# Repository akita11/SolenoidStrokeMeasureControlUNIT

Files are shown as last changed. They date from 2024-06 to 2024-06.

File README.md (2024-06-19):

# SolenoidStokeMeasureControl UNIT

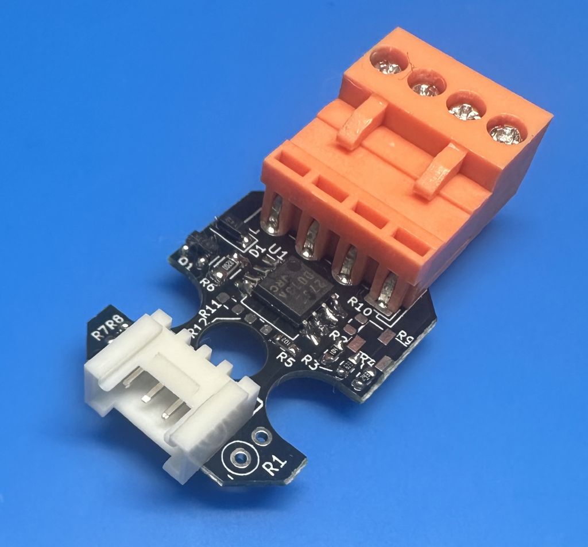
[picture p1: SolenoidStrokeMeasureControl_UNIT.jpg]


ソレノイドのストローク位置によってインダクタンスが変化し、PWM制御時の電流波形が変化することを利用して、ソレノイドのPWM制御とストローク位置の計測（推定）を同時に行うための回路です。
（基板形状が「[M5Stack用VH3.96-4ピンユニット[U020]](https://www.switch-science.com/products/4055)」と同一のため、そのケースを使うことができます。）

**【注意：重要】**
実際の制御・計測の動作には、ソレノイドごとに特性の計測を行う必要があり、また特性の個体差、温度特性なども考慮する必要があります。そのため、**「これを使ってサンプルプログラムを書き込めば間違いなく動作する（制御ができる）」というものではなく、あくまでもこの原理検証の実験のための回路**ということをご理解ください。測定原理やサンプルプログラムは[こちら](https://github.com/akita11/SolenoidStrokeMeasureControl)に適宜まとめて更新していきます。

## 使い方

オレンジ色のコネクタ(VH3.96-4p)に、ソレノイド用の電源とソレノイドを接続します。M5Stackの[BAVGソケット](https://www.switch-science.com/products/7234)を使うと、電源は2.1mmプラグ、負荷はスプリング端子で接続できて便利です。

Grove端子の3番("PWM"と表記）にPWM波形を加えてソレノイドをPWM駆動し、その駆動電流が電圧波形としてGrove端子の4番（"ADC"と表記）に出力されます。

なおArduinoやM5Stack (Core2/CoreS3)用のサンプルプログラムは[こちら](https://github.com/akita11/SolenoidStrokeMeasureControl)にあります（あくまでも参考用のものです）。Measure_...がパラメータ計測用のプログラム、Control...が位置計測（推定）・位置制御用のプログラムです。（ESP32用はM5Stack Core2のPortAに本ボードを接続して使用します）

### 増幅率の調整

ソレノイドの駆動電流を0.2Ωの抵抗で電圧変換し、それをオペアンプ（非反転増幅回路）で増幅して"ADC"端子に出力しています。その増幅率は、用いるソレノイド・電源電圧からきまる駆動電流にあわせて、適切な範囲に調整する必要があります。"ADC"端子の波形をオシロ等で計測し、用いるマイコンのADCの入力電圧範囲に収まるように増幅率を調整します。増幅率は基板裏面のハンダジャンパJP3/JP4JP5で調整できます。（JP3は初期状態でONになっていますので、OFFにする場合はパターンをカットしてください）

- JP3/JP4/JP5=ON/OFF/OFF : 101倍
- JP3/JP4/JP5=ON/ON/OFF : 39倍
- JP3/JP4/JP5=ON/OFF/ON : 20倍
- JP3/JP4/JP5=ON/ON/ON : 16倍
- JP3/JP4/JP5=OFF/OFF/OFF : R1にとりつける抵抗から決まる倍率（(R1÷1[kΩ]+1)倍）

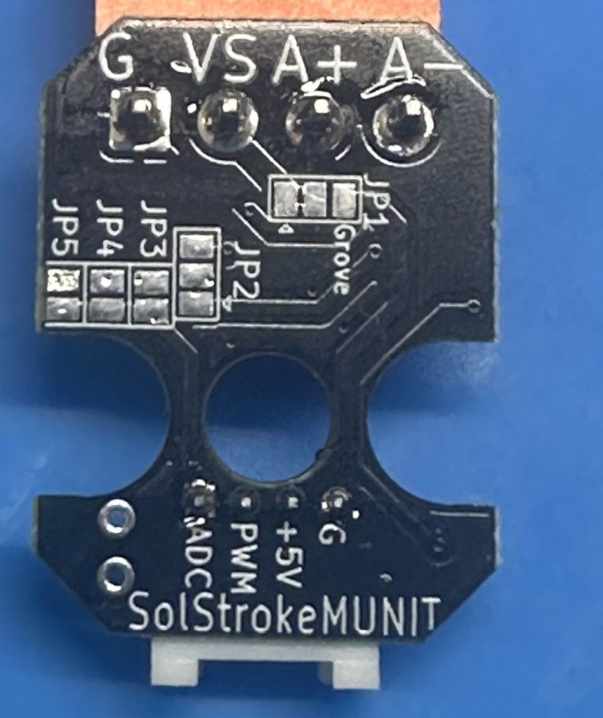
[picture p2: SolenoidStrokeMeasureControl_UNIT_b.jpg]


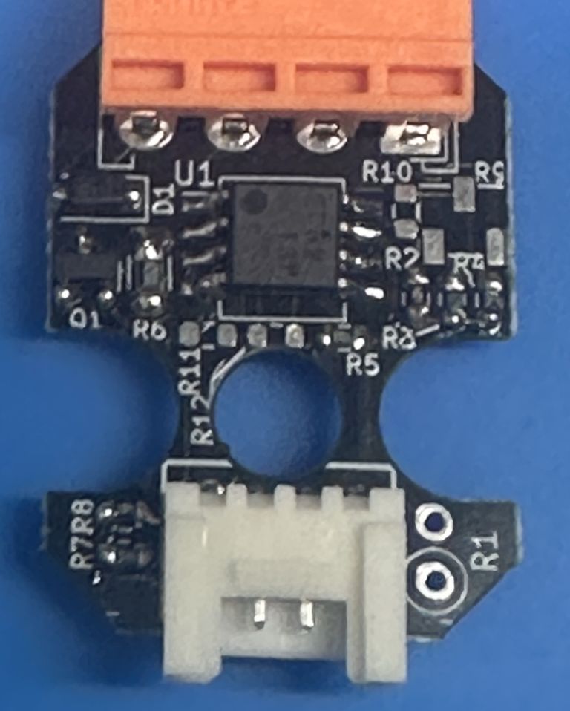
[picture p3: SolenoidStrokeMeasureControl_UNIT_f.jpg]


## 測定原理

ソレノイドは電気回路的にはインダクタで、そのインダクタンスはストローク（プランジャ）位置で変化します。そのためON時の充電電流の波形は、ストローク位置で変化します。ただし充電開始時の電流はOFF期間中の放電特性できまるため、ゼロからとは限りません。またPWMのON時間（PWMのデューティー比）によっても波形は変化します。

ソレノイドによっては、ON後の2箇所の時点（例えば100us後と700us後）での電流の差が、PWMのON時間（PWMのデューティー比）ごとにストローク位置に伴って変化するため、与えているPWM ON時間とその電流差から、ストローク位置を計測（推定）することができます。現時点で試した範囲では、TakahaのCBS0730シリーズはこの特性をもっています。（詳細は[arXivの論文](https://arxiv.org/abs/2405.11721)にまとめてあります）

ただしソレノイドによっては、この電流差がストロークによってほとんど変化しないため、この方法では位置を計測することができません。そのため、複数点の電流の計測値から、予め計測した位置と電流値との差（の総和）が最小となるように反復計算で位置を求めるアルゴリズムを開発中です。まだ安定性や精度の検証は不十分ですが、参考用に上記GitHubにArduinoとESP32用のソースコードをおいてあります（計測データはTakahaのLongStrokeSolenoidのもの）。

## Author

Junichi Akita (akita@ifdl.jp, @akita11)

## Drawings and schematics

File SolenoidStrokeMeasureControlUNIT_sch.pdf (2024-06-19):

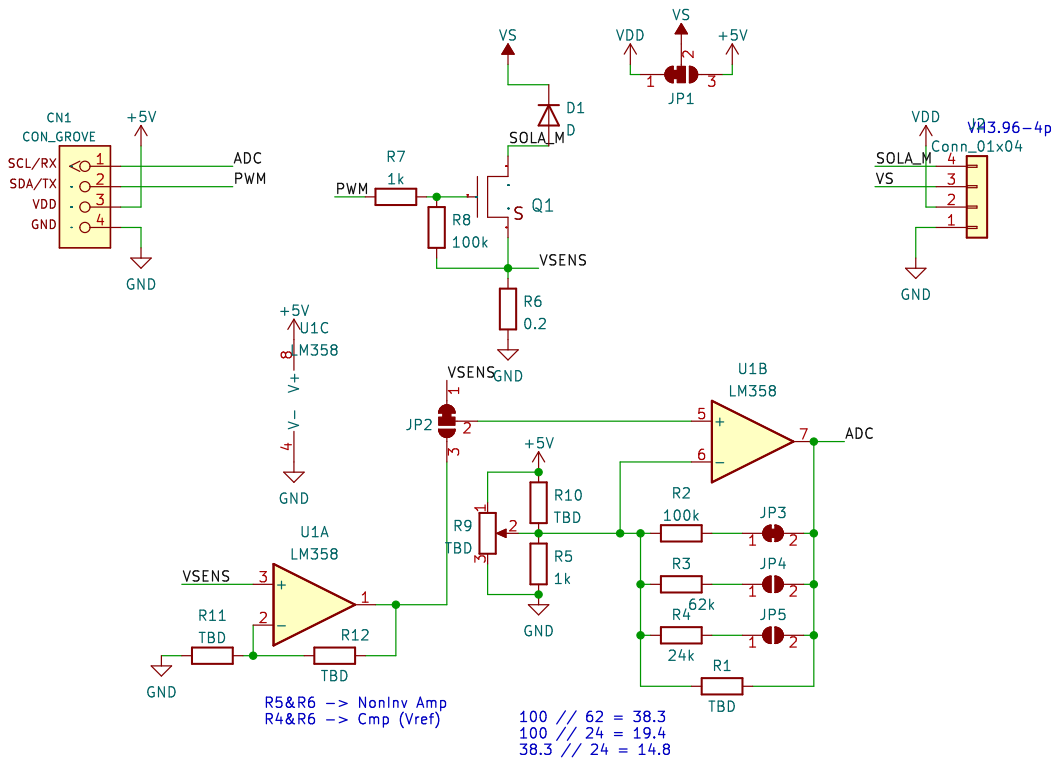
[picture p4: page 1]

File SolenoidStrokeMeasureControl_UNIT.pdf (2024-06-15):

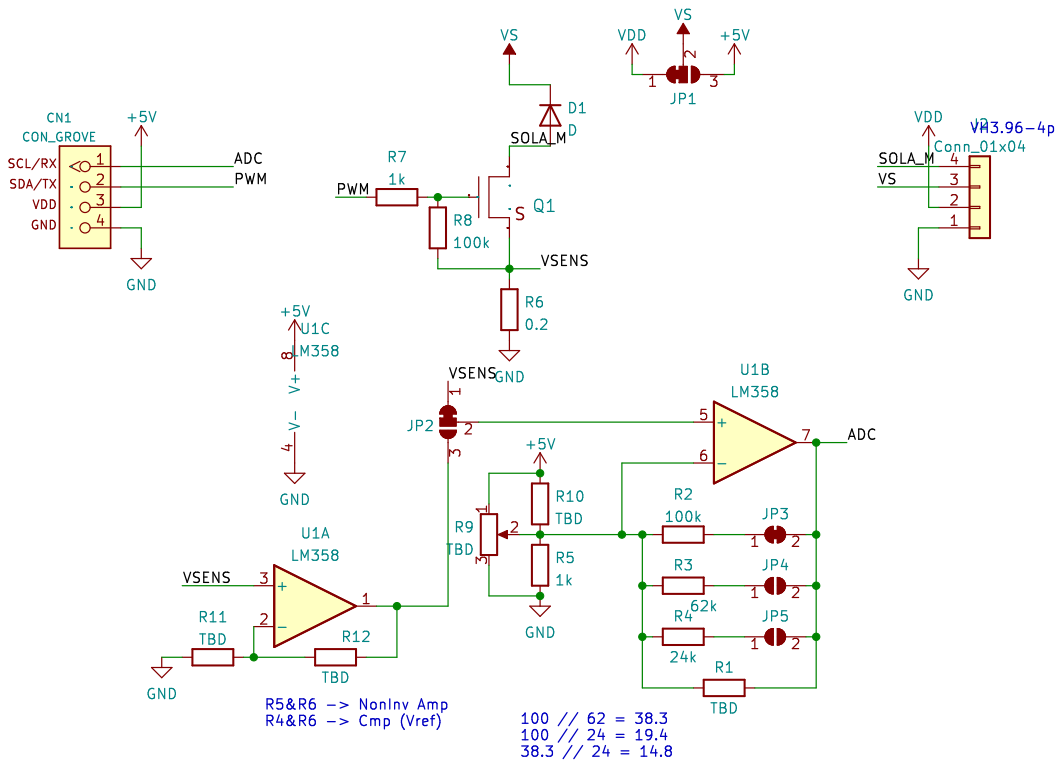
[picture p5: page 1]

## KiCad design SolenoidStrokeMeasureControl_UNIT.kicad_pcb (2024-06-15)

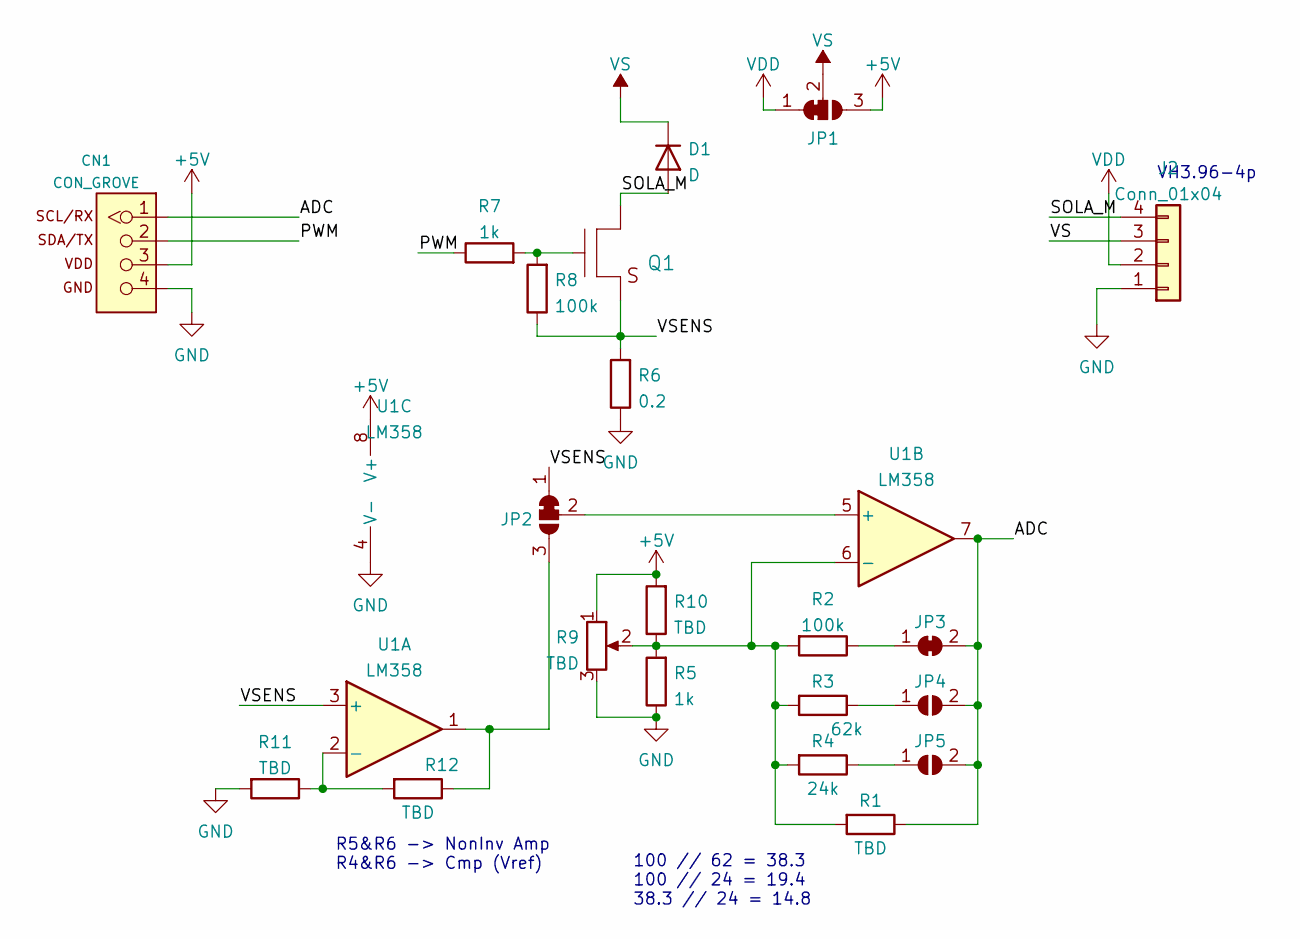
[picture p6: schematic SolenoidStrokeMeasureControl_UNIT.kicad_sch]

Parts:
CN1: CON_GROVE; CON_GROVE_H
D1: D; D_SOD-123F
J2: Conn_01x04; JST_VH_S4P-VH_1x04_P3.96mm_Horizontal
JP1, JP2: SolderJumper_3_Bridged12; SolderJumper-3_P1.3mm_Bridged2Bar12_Pad1.0x1.5mm
JP3: SolderJumper_2_Bridged; SolderJumper-2_P1.3mm_Bridged_Pad1.0x1.5mm
JP4, JP5: SolderJumper_2_Open; SolderJumper-2_P1.3mm_Open_Pad1.0x1.5mm
Q1: TR_NMOS_IRLML6344; SOT-23
R1: TBD; R_Axial_DIN0207_L6.3mm_D2.5mm_P2.54mm_Vertical
R2, R8: 100k; R_0603_1608Metric
R3: 62k; R_0603_1608Metric
R4: 24k; R_0603_1608Metric
R5, R7: 1k; R_0603_1608Metric
R6: 0.2; R_1206_3216Metric
R9: TBD; Potentiometer_Bourns_3223W
R10, R11, R12: TBD; R_0603_1608Metric
U1: LM358; SO-8_5.3x6.2mm_P1.27mm

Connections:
+5V: CN1.3, JP1.3 (B), R9.1, R10.2, U1.8 (V+)
/ADC: CN1.1, JP3.2 (B), JP4.2 (B), JP5.2 (B), R1.1, U1.7
/PWM: CN1.2, R7.1
/SOLA_M: D1.2 (A), J2.4, Q1.3 (D)
/VSENS: JP2.1 (A), Q1.2 (S), R6.2, R8.1, U1.3 (+)
GND: CN1.4, J2.1, R5.1, R6.1, R9.3, R11.2, U1.4 (V-)
unnamed: JP2.2 (C), U1.5 (+)
unnamed: JP2.3 (B), R12.1, U1.1
unnamed: JP4.1 (A), R3.1
unnamed: JP5.1 (A), R4.1
unnamed: Q1.1 (G), R7.2, R8.2
unnamed: JP3.1 (A), R2.1
unnamed: R1.2, R2.2, R3.2, R4.2, R5.2, R9.2, R10.1, U1.6 (-)
unnamed: R11.1, R12.2, U1.2 (-)
VDD: J2.2, JP1.1 (A)
VS: D1.1 (K), J2.3, JP1.2 (C)

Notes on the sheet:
100 // 62 = 38.3 100 // 24 = 19.4 38.3 // 24 = 14.8
R5&R6 -> NonInv Amp R4&R6 -> Cmp (Vref)
VH3.96-4p

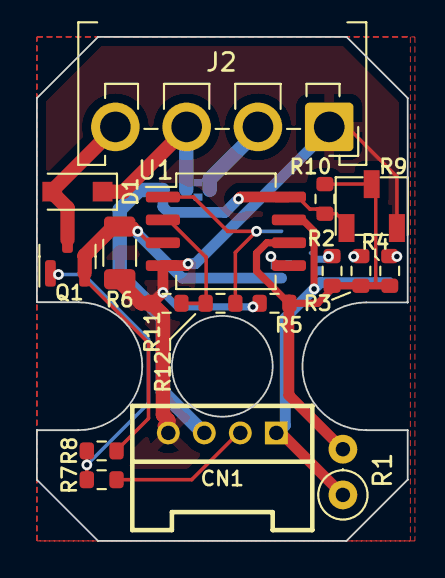
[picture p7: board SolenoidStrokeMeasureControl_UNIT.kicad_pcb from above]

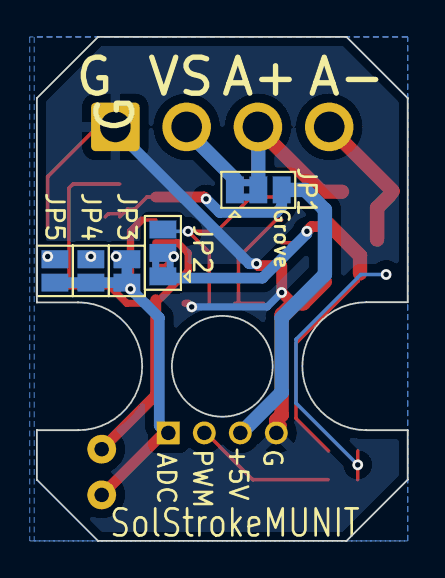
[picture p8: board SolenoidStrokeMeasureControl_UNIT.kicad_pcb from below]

Board: 2 copper layers, 20.6 x 28.0 mm, 22 parts (5 on the bottom side), 16 nets.
